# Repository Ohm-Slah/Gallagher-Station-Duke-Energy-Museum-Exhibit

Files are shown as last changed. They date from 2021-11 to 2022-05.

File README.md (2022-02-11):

# Gallagher-Station-Museum-Exhibit
 

A code repository for the Duke Energy funded exhibit at the Padgett Museum of the Gallagher Station, created by Purdue Polytechnic SoET students. This repository is only for the use of and contributed by these students. However, this information is for public viewing and usage. Any unwarranted pull-requests from unathorized individuals will be rejected, as this is to document the final product as-is. All code is under no licensure and is open for usage in the public domain. 

0607_ky_gallagher_station_plant

# What is this?
The Duke Energy Gallagher Station is located in New Albany, IN, and was a power generating facility that was of tremendous aid in powering Southern Indiana from 1958 until decommissioning in June of 2021. Duke Energy proposed the creation of an interactive museum exhibit representing the operation of a coal-fired power plant, with focus on the control system within the display. 

This project will be located at the Padgett Museum in New Albany, IN. The showcase will educate users on energy production control using older and current technologies and incorporating donated equipment from the Gallagher Station. The interactive exhibit will primarily be used by senior museum guests during normal operating hours of the Padgett Museum for an average of XX amount of time, and will not require training or previous knowledge of power systems to interact with it. This project must safely fit into the designated area of the museum without obstructing walking paths or needing to modify the surrounding environment. This project must be capable of being moved to a school and interacted with by a younger audience.

The code running on the Arduino Mega was written on a VSCode environment compiled and linked with the extension PlatformIO.

The code running on the ATTiny4313 controlling the 7-segment display is writen, compiled, and linked in the Arduino IDE.

# Folder Structure
The [src folder](https://github.com/Ohm-Slah/Gallagher-Station-Duke-Energy-Museum-Exhibit/tree/main/src) contains all cpp files to run on the Arduino Mega.

The [include folder](https://github.com/Ohm-Slah/Gallagher-Station-Duke-Energy-Museum-Exhibit/tree/main/include) contains all c header files used on Arduino Mega.

The [pi folder](https://github.com/Ohm-Slah/Gallagher-Station-Duke-Energy-Museum-Exhibit/tree/main/pi) contains the python code running on the raspberry pi.

The [pictures folder](https://github.com/Ohm-Slah/Gallagher-Station-Duke-Energy-Museum-Exhibit/tree/main/Pictures) contains pictures used in this repository.

The proc folder is no longer used, but is there for reference from another version of code on the Raspberry Pi.

# Proof of Concept Prototype
The proof of [concept prototype code](https://github.com/Ohm-Slah/Gallagher-Station-Duke-Energy-Museum-Exhibit/tree/Proof-of-Concept-Prototype) has been left as a seperate branch in Github, and you can view the project as how it was before any polish whatsoever. In the proof of concept for the method of playing videos at the request of a microcontroller, the program chosen initially was processing3 on Raspberry Pi. This was written in Java and worked well on a PC, however when running on a Raspberry Pi, the framerate dipped drastically. After a great deal of debugging and research, the final decision was to use OMXPlayer on Raspberry Pi programmed in Python. This switch to OMXPlayer was not realized until after the proof of concept prototype.
The proof of concept was also only programmed initially to showcase a rudimentary version of phases 0, 1, & 2, as well as the failure and completion routines. This code also showed the functionality of a stepper motor designed into a donated Gallagher Station gauge in place of a phase 3. There was no phase 4 written.

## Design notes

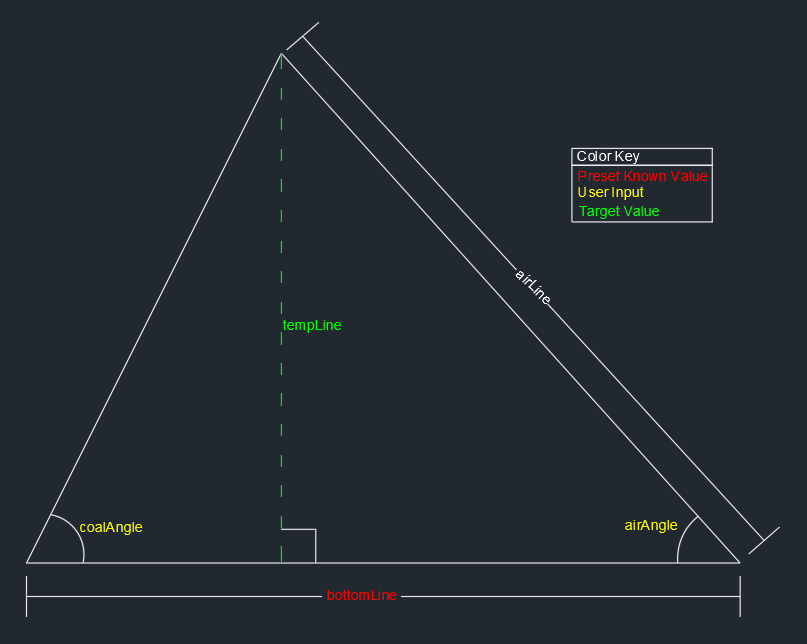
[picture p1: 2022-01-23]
Pictures/phase_one_conceptual.png

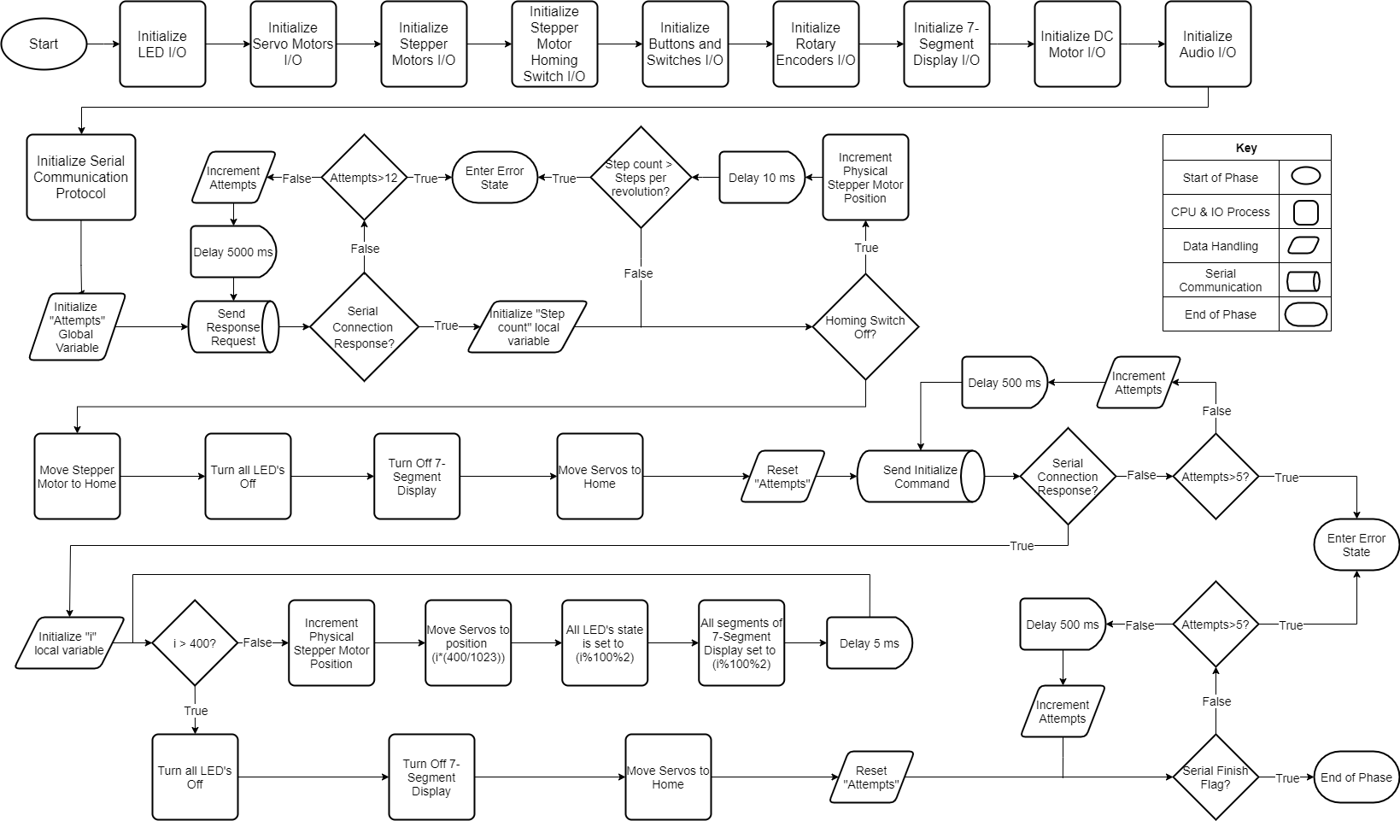
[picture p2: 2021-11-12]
Pictures/Gallagher_Code_Flow_Chart-Initialization.drawio.png

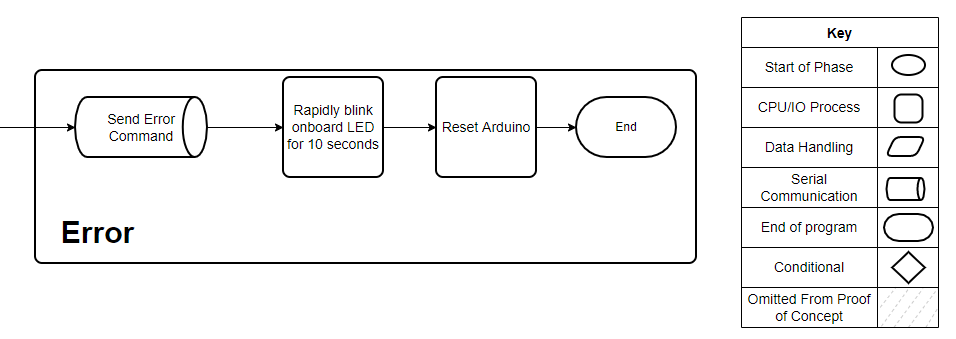
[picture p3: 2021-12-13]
Pictures/flowerror.PNG

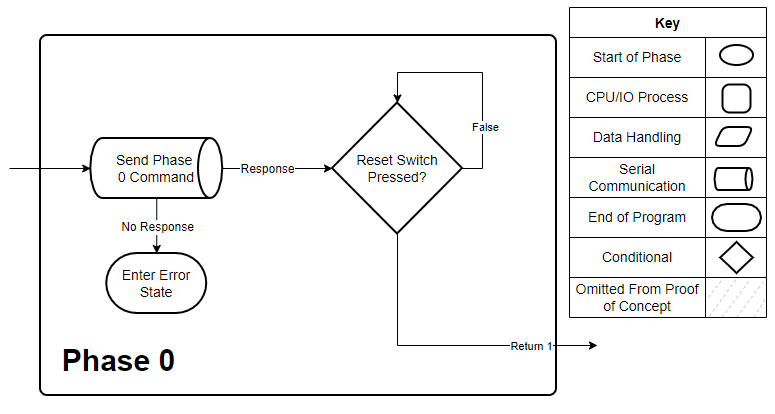
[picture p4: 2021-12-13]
Pictures/flowp0.PNG

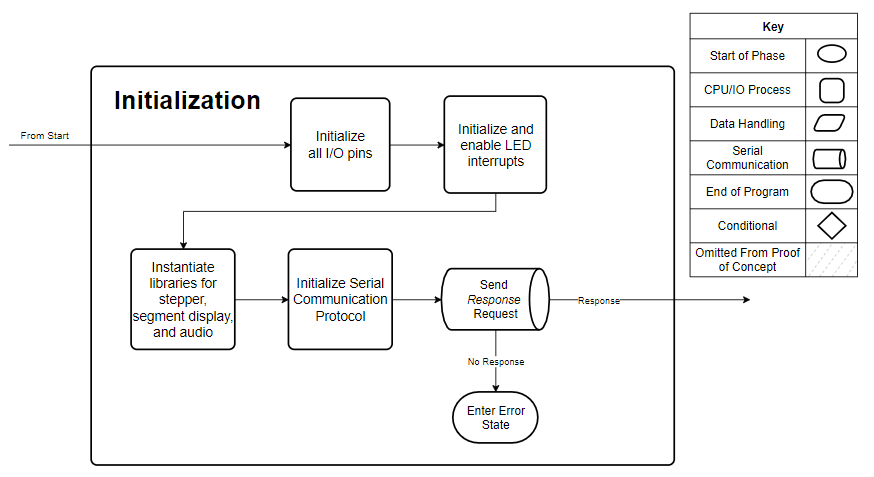
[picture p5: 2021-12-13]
Pictures/flowinit.PNG

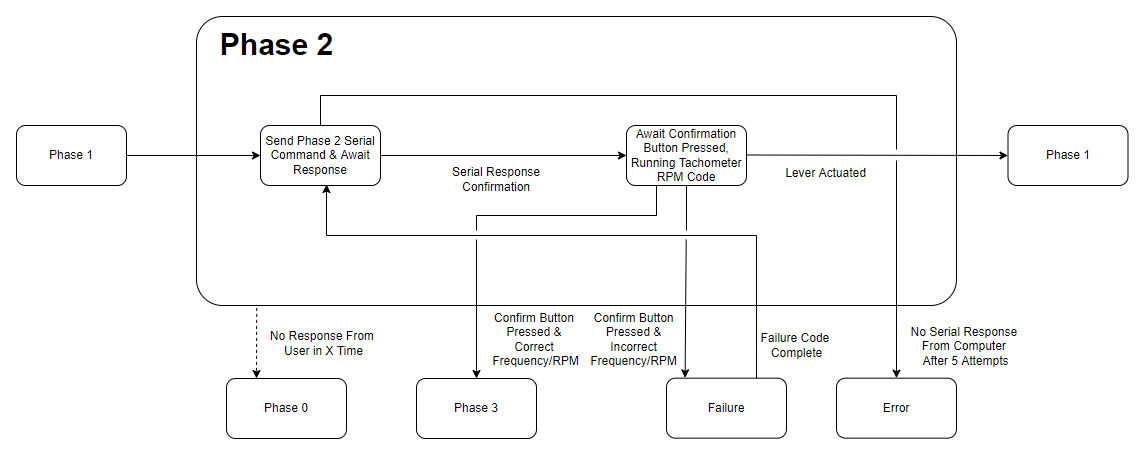
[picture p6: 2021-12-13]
Pictures/stphase2.PNG

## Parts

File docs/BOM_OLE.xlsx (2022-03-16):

 |  |  |  | DWG 1110 BILL OF MATERIALS (BOM)
DWG 1100 BILL OF MATERIALS (BOM) |  |  |  | IDENTIFIER | DESCRIPTION | PART #
IDENTIFIER | DESCRIPTION | PART # | LINK | M1 | SERVO MOTOR | SER-M-001
U1 | ARDUINO MEGA 2560 ATMEGA2560 | A000067 | https://www.digikey.com/en/products/detail/arduino/A000067/2639006 | M2 | SERVO MOTOR | SER-M-001
U2 | MICRO-SD CARD MODULE FOR ARDUINO | DFR0229 | https://www.digikey.com/en/products/detail/dfrobot/DFR0229/6588460 | U4 | ROTARY ENCODER | 288T232R161A1
J1 | CONN HEADER VERT 12POS 2.5MM | 533751210 | https://www.digikey.com/en/products/detail/molex/0533751210/3263206?s=N4IgTCBcDaIAwFYDMSDsCCMYNxAXQF8g | U5 | ROTARY ENCODER | 288T232R161A1
J23 | CONN HEADER VERT 11POS 2.5MM | 533751110 | https://www.digikey.com/en/products/detail/molex/0533751110/3263205?s=N4IgTCBcDaIAwFYDMSDsCCMW4gLoF8g | U6 | ROTARY ENCODER | 288T232R161A1
J6 | CONN HEADER VERT 7POS 2.5MM | 533750710 | https://www.digikey.com/en/products/detail/molex/0533750710/2421228?s=N4IgTCBcDaIAwFYDMSDsC6oIxxAXQF8g | U7 | ROTARY ENCODER | 288T232R161A1
J9 | CONN HEADER VERT 7POS 2.5MM | 533750710 | https://www.digikey.com/en/products/detail/molex/0533750710/2421228?s=N4IgTCBcDaIAwFYDMSDsC6oIxxAXQF8g | J2 | 3-PIN MALE MOLEX CONNECTOR | 3-M-MOLEX
J41 | CONN HEADER VERT 5POS 2.5MM | 533750510 | https://www.digikey.com/en/products/detail/molex/0533750510/2421211?s=N4IgTCBcDaIAwFYDMSDsDEEY4gLoF8g | J3 | 3-PIN MALE MOLEX CONNECTOR | 3-M-MOLEX
J15 | CONN HEADER VERT 2POS 2.5MM | 533750210 | https://www.digikey.com/en/products/detail/molex/0533750210/2405348?s=N4IgTCBcDaIAwFYDMSDsC5gIxxAXQF8g | J4 | 3-PIN MALE MOLEX CONNECTOR | 3-M-MOLEX
J47 | CONN HEADER VERT 2POS 2.5MM | 533750210 | https://www.digikey.com/en/products/detail/molex/0533750210/2405348?s=N4IgTCBcDaIAwFYDMSDsC5gIxxAXQF8g | J5 | 3-PIN MALE MOLEX CONNECTOR | 3-M-MOLEX
J27 | CONN HEADER VERT 2POS 2.5MM | 533750210 | https://www.digikey.com/en/products/detail/molex/0533750210/2405348?s=N4IgTCBcDaIAwFYDMSDsC5gIxxAXQF8g | J7 | 3-PIN MALE MOLEX CONNECTOR | 3-M-MOLEX
J29 | CONN HEADER VERT 2POS 2.5MM | 533750210 | https://www.digikey.com/en/products/detail/molex/0533750210/2405348?s=N4IgTCBcDaIAwFYDMSDsC5gIxxAXQF8g | J8 | 3-PIN MALE MOLEX CONNECTOR | 3-M-MOLEX
J31 | CONN HEADER VERT 2POS 2.5MM | 533750210 | https://www.digikey.com/en/products/detail/molex/0533750210/2405348?s=N4IgTCBcDaIAwFYDMSDsC5gIxxAXQF8g | CABLE_001 | REFFERENCE DRAWING 1120
J48 | CONN HEADER VERT 2POS 2.5MM | 533750210 | https://www.digikey.com/en/products/detail/molex/0533750210/2405348?s=N4IgTCBcDaIAwFYDMSDsC5gIxxAXQF8g | CABLE_003 | REFFERENCE DRAWING 1120
J33 | CONN HEADER VERT 2POS 2.5MM | 533750210 | https://www.digikey.com/en/products/detail/molex/0533750210/2405348?s=N4IgTCBcDaIAwFYDMSDsC5gIxxAXQF8g
H1 | HEX STANDOFF THREADED M2.5 | 971050154 | https://www.digikey.com/en/products/detail/würth-elektronik/971050154/9488600 | DWG 1111 BILL OF MATERIALS (BOM)
H2 | HEX STANDOFF THREADED M2.6 | 971050154 | https://www.digikey.com/en/products/detail/würth-elektronik/971050154/9488600 | IDENTIFIER | DESCRIPTION | PART #
H3 | HEX STANDOFF THREADED M2.7 | 971050154 | https://www.digikey.com/en/products/detail/würth-elektronik/971050154/9488600 | J28 | 2-PIN MALE MOLEX CONNECTOR | 2-M-MOLEX
H4 | HEX STANDOFF THREADED M2.8 | 971050154 | https://www.digikey.com/en/products/detail/würth-elektronik/971050154/9488600 | J30 | 2-PIN MALE MOLEX CONNECTOR | 2-M-MOLEX
U3 | CUSTOM JLC PCB | JLC01 | https://www.digikey.com/en/products/detail/molex/0533750210/2405348?s=N4IgTCBcDaIAwFYDMSDsC5gIxxAXQF8g | J32 | 2-PIN MALE MOLEX CONNECTOR | 2-M-MOLEX
CABLE_001 | REFFERENCE DRAWING 1120 |  |  | J49 | 2-PIN MALE MOLEX CONNECTOR | 2-M-MOLEX
CABLE_002 | REFFERENCE DRAWING 1120 |  |  | S1 | NO-PUSH BUTTON | PB-001
CABLE_003 | REFFERENCE DRAWING 1120 |  |  | S2 | NO-PUSH BUTTON | PB-002
CABLE_006 | REFFERENCE DRAWING 1121 |  |  | S3 | NO-PUSH BUTTON | PB-003
CABLE_010 | REFFERENCE DRAWING 1121 |  |  | S4 | NO-PUSH BUTTON | PB-004
CABLE_012 | REFFERENCE DRAWING 1121 |  |  | CABLE_012 | REFFERENCE DRAWING 1121
CABLE_013 | REFFERENCE DRAWING 1122 |  |  | CABLE_013 | REFFERENCE DRAWING 1122
CABLE_014 | REFFERENCE DRAWING 1122 |  |  | CABLE_014 | REFFERENCE DRAWING 1122
CABLE_015 | REFFERENCE DRAWING 1122 |  |  | CABLE_022 | REFFERENCE DRAWING 1123
CABLE_018 | REFFERENCE DRAWING 1122
CABLE_021 | REFFERENCE DRAWING 1123 |  |  | DWG 1610 BILL OF MATERIALS (BOM)
CABLE_022 | REFFERENCE DRAWING 1123 |  |  | IDENTIFIER | DESCRIPTION | PART #
 |  |  |  | J37 | 2-PIN MALE MOLEX CONNECTOR | 2-M-MOLEX
 | DWG 1120 BILL OF MATERIALS (BOM) |  |  | DS1 | 60W LED LIGHT-BULB | LED-60
IDENTIFIER | DESCRIPTION | PART # |  | CABLE_016 | REFFERENCE DRAWING 1620
J1 | 12-PIN ON-BOARD MALE CRIMP CONNECTOR | 51163-1200 |  | CABLE_017 | REFFERENCE DRAWING 1620
J2 | 3-PIN FEMALE MOLEX CONNECTOR | 3-F-MOLEX |  | DWG 1210 BILL OF MATERIALS (BOM)
J3 | 3-PIN FEMALE MOLEX CONNECTOR | 3-F-MOLEX |  | IDENTIFIER | DESCRIPTION | PART #
J4 | 3-PIN FEMALE MOLEX CONNECTOR | 3-F-MOLEX |  | U7 | HOMING SWITCH | Z6535-ND
J5 | 3-PIN FEMALE MOLEX CONNECTOR | 3-F-MOLEX |  | J14 | 4-PIN MALE MOLEX CONNECTOR | 4-M-MOLEX
J6 | 7-PIN ON-BOARD MALE CRIMP CONNECTOR | 53375-0710 |  | J12 | 7-PIN MALE MOLEX CONNECTOR | 7-M-MOLEX
J7 | 3-PIN FEMALE MOLEX CONNECTOR | 3-F-MOLEX |  | M3 | DC MOTOR | 2790-PC280LG-302-ND
J8 | 3-PIN FEMALE MOLEX CONNECTOR | 3-F-MOLEX |  | M4 | STEPPER MOTOR | 1568-1105-ND
J9 | 7-PIN ON-BOARD MALE CRIMP CONNECTOR | 53375-0710 |  | CABLE_004 | REFFERENCE DRAWING 1220
J10 | 7-PIN ON-BOARD FEMALE CRIMP CONNECTOR | 51163-0700 |  | CABLE_005 | REFFERENCE DRAWING 1220
 | DWG 1121 BILL OF MATERIALS (BOM) |  |  | DWG 1510 BILL OF MATERIALS (BOM)
IDENTIFIER | DESCRIPTION | PART # |  | IDENTIFIER | DESCRIPTION | PART #
J15 | 2-Pin MALE MOLEX MINI-LOCK CONNECTOR | 53375-0210 |  | J18 | 2-PIN MALE MOLEX CONNECTOR | 2-M-MOLEX
J16 | 2-PIN FEMALE MOLEX CONNECTOR | 2-F-MOLEX |  | J20 | 2-PIN MALE MOLEX CONNECTOR | 2-M-MOLEX
J23 | 11-PIN MALE MOLEX MINI-LOCK CONNECTOR | 53375-1210 |  | J22 | 2-PIN MALE MOLEX CONNECTOR | 2-M-MOLEX
J24 | 11-PIN FEMALE MOLEX CONNECTOR | 11-F-MOLEX |  | LS1 | VISATON 8-OHM SPEAKER | K 64 WP - 8 OHM
J27 | 2-PIN MALE MOLEX MINI-LOCK CONNECTOR | 53375-0210 |  | LS2 | VISATON 8-OHM SPEAKER | K 64 WP - 8 OHM
J28 | 2-PIN FEMALE MOLEX CONNECTOR | 2-F-MOLEX |  | LS3 | VISATON 8-OHM SPEAKER | K 64 WP - 8 OHM
 |  |  |  | CABLE_007 | REFFERENCE DRAWING 1520
 | DWG 1122 BILL OF MATERIALS (BOM) |  |  | CABLE_008 | REFFERENCE DRAWING 1520
IDENTIFIER | DESCRIPTION | PART # |  | CABLE_009 | REFFERENCE DRAWING 1520
J29 | 2-PIN ON-BOARD MALE CRIMP CONNECTOR | 53375-0210
J30 | 2-PIN FEMALE MOLEX CONNECTOR | 2-F-MOLEX |  | DWG 1210 BILL OF MATERIALS (BOM)
J31 | 2-PIN ON-BOARD MALE CRIMP CONNECTOR | 53375-0210 |  | IDENTIFIER | DESCRIPTION | PART #
J32 | 2-PIN FEMALE MOLEX CONNECTOR | 2-F-MOLEX |  | U7 | OMRON ELECTRONICS HOMING SWITCH | EE-SX4162-P1-Z
J33 | 2-PIN ON-BOARD MALE CRIMP CONNECTOR | 53375-0210 |  | J14 | 2-PIN FEMALE MOLEX CONNECTOR | 2-F-MOLEX
J34 | 2-PIN FEMALE MOLEX CONNECTOR | 2-F-MOLEX |  | J12 | 4-PIN FEMALE MOLEX CONNECTOR | 4-F-MOLEX
J41 | 5-PIN ON-BOARD MALE CRIMP CONNECTOR | 53375-0510 |  | J51 | 3-PIN FEMALE MOLEX CONNECTOR | 3-F-MOLEX
J42 | 5-PIN FEMALE MOLEX CONNECTOR | 5-F-MOLEX |  | M3 | JOHNSON MOTOR DC MOTOR | PC280LG-302
 |  |  |  | M4 | SPARKFUN STEPPER MOTOR | ROB-09238
 | DWG 1123 BILL OF MATERIALS (BOM) |  |  | CABLE_004 | REFFERENCE DRAWING 1220
IDENTIFIER | DESCRIPTION | PART # |  | CABLE_005 | REFFERENCE DRAWING 1220
J46 | 2-PIN MALE MOLEX MINI-LOCK CONNECTOR | 53375-0210
J47 | 2-PIN FEMALE MOLEX CONNECTOR | 2-F-MOLEX |  | DWG 1110 BILL OF MATERIALS (BOM)
J48 | 2-PIN MALE MOLEX MINI-LOCK CONNECTOR | 53375-0210 |  | IDENTIFIER | DESCRIPTION | PART #
J49 | 2-PIN FEMALE MOLEX CONNECTOR | 2-F-MOLEX |  | M1 | ADAFRUIT SERVO MOTOR | 154
 |  |  |  | M2 | ADAFRUIT SERVO MOTOR | 154
DWG 1200 BILL OF MATERIALS (BOM) |  |  |  | U4 | CTS ELECTRONICS ROTARY ENCODER | 288T232R161A1
IDENTIFIER | DESCRIPTION | PART # | LINK | U5 | CTS ELECTRONICS ROTARY ENCODER | 288T232R161A1
U4 | DRV8801 DC MOTOR DRIVER CARRIER | 2136 | https://www.digikey.com/en/products/detail/pololu-corporation/2136/10450430?s=N4IgTCBcDaICICUBqAOFAGAjCAugXyA | U6 | CTS ELECTRONICS ROTARY ENCODER | 288T232R161A1
U5 | A4988 STEPPER DRIVER | 1182 | https://www.digikey.com/en/products/detail/pololu-corporation/1182/10450403 | U7 | CTS ELECTRONICS ROTARY ENCODER | 288T232R161A1
U6 | CUSTOM JLC PCB | JLC02 |  | J2 | 3-PIN MALE MOLEX CONNECTOR | 3-M-MOLEX
J11 | CONN HEADER VERT 7POS 2.5MM | 533750710 | https://www.digikey.com/en/products/detail/molex/0533750710/2421228?s=N4IgTCBcDaIAwFYDMSDsC6oIxxAXQF8g | J3 | 3-PIN MALE MOLEX CONNECTOR | 3-M-MOLEX
J10 | CONN HEADER VERT 7POS 2.5MM | 533750710 | https://www.digikey.com/en/products/detail/molex/0533750710/2421228?s=N4IgTCBcDaIAwFYDMSDsC6oIxxAXQF8g | J4 | 3-PIN MALE MOLEX CONNECTOR | 3-M-MOLEX
J13 | CONN HEADER VERT 2POS 2.5MM | 533750210 | https://www.digikey.com/en/products/detail/molex/0533750210/2405348?s=N4IgTCBcDaIAwFYDMSDsC5gIxxAXQF8g | J5 | 3-PIN MALE MOLEX CONNECTOR | 3-M-MOLEX
J43 | CONN HEADER VERT 5POS 2.5MM | 533750510 | https://www.digikey.com/en/products/detail/molex/0533750510/2421211?s=N4IgTCBcDaIAwFYDMSDsDEEY4gLoF8g | J7 | 3-PIN MALE MOLEX CONNECTOR | 3-M-MOLEX
H1 | HEX STANDOFF THREADED M2.5 | 971050154 | https://www.digikey.com/en/products/detail/würth-elektronik/971050154/9488600 | J8 | 3-PIN MALE MOLEX CONNECTOR | 3-M-MOLEX
H2 | HEX STANDOFF THREADED M2.5 | 971050154 | https://www.digikey.com/en/products/detail/würth-elektronik/971050154/9488600 | CABLE_001 | REFFERENCE DRAWING 1120
H3 | HEX STANDOFF THREADED M2.5 | 971050154 | https://www.digikey.com/en/products/detail/würth-elektronik/971050154/9488600 | CABLE_003 | REFFERENCE DRAWING 1120
H4 | HEX STANDOFF THREADED M2.5 | 971050154 | https://www.digikey.com/en/products/detail/würth-elektronik/971050154/9488600
CABLE_002 | REFFERENCE DRAWING 1120
CABLE_004 | REFFERENCE DRAWING 1220
CABLE_005 | REFFERENCE DRAWING 1220
CABLE_019 | REFFERENCE DRAWING 1220
 | DWG 1220 BILL OF MATERIALS (BOM)
IDENTIFIER | DESCRIPTION | PART #
J11 | 7-PIN MALE MOLEX MINI-LOCK CONECTOR | 53375-0710
J12 | 4-PIN FEMALE MOLEX CONNECTOR | 4-F-MOLEX
J51 | 3-PIN FEMALE MOLEX CONNECTOR | 3-F-MOLEX
J13 | 2-PIN MALE MOLEX MINI-LOCK CONECTOR | 53375-0210
J14 | 4-PIN FEMALE MOLEX CONNECTOR | 4-F-MOLEX
J40 | 5-PIN MALE MOLEX MINI-LOCK CONECTOR | 53375-0510
J43 | 5-PIN FEMALE MOLEX CONNECTOR | 5-F-MOLEX
DWG 1300 BILL OF MATERIALS (BOM)
IDENTIFIER | DESCRIPTION | PART # | LINK
U7 | AVR SERIES MICROCONTROLLER IC 8-BIT | ATTINY4313-PU | https://www.digikey.com/en/products/detail/microchip-technology/ATTINY4313-PU/2271083
U8 | UNIQUE GALLAGHER STATION 7-SEGMENT PASSIVE DISPLAY BOARD | GS-7-SEG
U9 | CUSTOM PROTO BOARD LAYOUT | 2670 | https://www.digikey.com/en/products/detail/adafruit-industries-llc/2670/7244957
J42 | CONNECTOR HEADER THROUGH HOLE 5 POSITION | 533750510 | https://www.digikey.com/en/products/detail/molex/0533750510/2421211?s=N4IgTCBcDaIAwFYDMSDsDEEY4gLoF8g
R1 -> R15 | 150 OHMS ±1% 0.6W THROUGH HOLE RESISTOR | LR1F150R | https://www.digikey.com/en/products/detail/te-connectivity-passive-product/LR1F150R/3477523
Q1 -> Q7 | BIPOLAR (BJT) TRANSISTOR NPN 40 V 600 mA | 2N2222A | https://www.digikey.com/en/products/detail/diotec-semiconductor/2N2222A/13575189
CABLE_018 | REFFERENCE DRAWING 1122
DWG 1400 BILL OF MATERIALS (BOM)
IDENTIFIER | DESCRIPTION | PART # | LINK
U10 | CUSTOM JLC PCB | JLC03
J26 | CONN HEADER VERT 2POS 2.5MM | 533750210 | https://www.digikey.com/en/products/detail/molex/0533750210/2405348?s=N4IgTCBcDaIAwFYDMSDsC5gIxxAXQF8g
J24 | CONN HEADER VERT 11POS 2.5MM | 533751110 | https://www.digikey.com/en/products/detail/molex/0533751110/3263205?s=N4IgTCBcDaIAwFYDMSDsCCMW4gLoF8g
J50 -> J60 | CONN HEADER VERT 2POS 2.5MM | 533750210 | https://www.digikey.com/en/products/detail/molex/0533750210/2405348?s=N4IgTCBcDaIAwFYDMSDsC5gIxxAXQF8g
H1 -> H4 | HEX STANDOFF THREADED M2.5 | 971050154 | https://www.digikey.com/en/products/detail/würth-elektronik/971050154/9488600
Q8 -> Q18 | TRANS PNP 40V 0.2A TO-92 | 2N3906 | https://www.digikey.com/en/products/detail/stmicroelectronics/2N3906/603429
R16 -> R26 | RES 1 KOHMS 1/2W AXIAL | 273-1.0K-RC | https://www.digikey.com/en/products/detail/xicon/273-1-0K-RC/10485991
R27 -> R37 | RES 220 OHMS 1/2W AXIAL | HWCC122 | https://www.digikey.com/en/products/detail/nte-electronics-inc/HWCC122/11654401
CABLE_010 | REFFERENCE DRAWING 1121
CABLE_011 | REFFERENCE DRAWING 1420
 | DWG 1420 BILL OF MATERIALS (BOM)
IDENTIFIER | DESCRIPTION | PART #
J25 | 2-PIN ON-BOARD MALE CRIMP CONNECTOR | 53375-0210
J26 | 2-PIN FEMALE MOLEX CONNECTOR | 2-F-MOLEX
DWG 1500 BILL OF MATERIALS (BOM)
IDENTIFIER | DESCRIPTION | PART # | LINK
U11 | AMP AUDIO 3.7W CLASS D | 987 | https://www.digikey.com/en/products/detail/adafruit-industries-llc/987/5629428
U12 | IC OPAMP GP 2 CIRCUIT 8DIP | LM358AN/NOPB | https://www.digikey.com/en/products/detail/texas-instruments/LM358AN-NOPB/54928
U13 | AUX CABLE TO BARE COPPER WIRES | AUX-01
U14 | CUSTOM JLC PCB | JLC04
C1 & C2 | CAP ALUM 100UF 20% 16V RADIAL | UPJ1C101MED1TD | https://www.digikey.com/en/products/detail/nichicon/UPJ1C101MED1TD/3129347
J16 | CONNECTOR HEADER THROUGH HOLE 2 POSITION | 533750210 | https://www.digikey.com/en/products/detail/molex/0533750210/2405348
J17 | CONNECTOR HEADER THROUGH HOLE 2 POSITION | 533750210 | https://www.digikey.com/en/products/detail/molex/0533750210/2405348
J19 | CONNECTOR HEADER THROUGH HOLE 2 POSITION | 533750210 | https://www.digikey.com/en/products/detail/molex/0533750210/2405348
J21 | CONNECTOR HEADER THROUGH HOLE 2 POSITION | 533750210 | https://www.digikey.com/en/products/detail/molex/0533750210/2405348
J45 | CONNECTOR HEADER THROUGH HOLE 5 POSITION | 533750510 | https://www.digikey.com/en/products/detail/molex/0533750510/2421211?s=N4IgTCBcDaIAwFYDMSDsDEEY4gLoF8g
H1 -> H4 | HEX STANDOFF THREADED M2.5 | 971050154 | https://www.digikey.com/en/products/detail/würth-elektronik/971050154/9488600
CABLE_006 | REFFERENCE DRAWING 1121
CABLE_007 | REFFERENCE DRAWING 1520
CABLE_008 | REFFERENCE DRAWING 1520
CABLE_009 | REFFERENCE DRAWING 1520
CABLE_020 | REFFERENCE DRAWING 1520
 | DWG 1520 BILL OF MATERIALS (BOM)
IDENTIFIER | DESCRIPTION | PART #
J17 | 2-PIN ON-BOARD MALE CRIMP CONNECTOR | 53375-0210
J18 | 2-PIN FEMALE MOLEX CONNECTOR | 2-F-MOLEX
J19 | 2-PIN ON-BOARD MALE CRIMP CONNECTOR | 53375-0210
J20 | 2-PIN FEMALE MOLEX CONNECTOR | 2-F-MOLEX
J21 | 2-PIN ON-BOARD MALE CRIMP CONNECTOR | 53375-0210
J22 | 2-PIN FEMALE MOLEX CONNECTOR | 2-F-MOLEX
J44 | 5-PIN ON-BOARD MALE CRIMP CONNECTOR | 53375-0510
J45 | 5-PIN FEMALE MOLEX CONNECTOR | 5-F-MOLEX
DWG 1600 BILL OF MATERIALS (BOM)
IDENTIFIER | DESCRIPTION | PART # | LINK
U15 | SOLID STATE RELAY | AQH3213
U16 | CUSTOM JLC PCB | JLC04
R38 | RES 120 OHM 1% 0.6W AXIAL | LR1F120R | https://www.digikey.com/en/products/detail/te-connectivity-passive-product/LR1F120R/3477521
J34 | CONNECTOR HEADER THROUGH HOLE 2 POSITION | 533750210 | https://www.digikey.com/en/products/detail/molex/0533750210/2405348
J36 | CONNECTOR HEADER THROUGH HOLE 2 POSITION | 533750210 | https://www.digikey.com/en/products/detail/molex/0533750210/2405348
J38 | CONNECTOR HEADER THROUGH HOLE 2 POSITION | 533750210 | https://www.digikey.com/en/products/detail/molex/0533750210/2405348
H1 -> H4 | HEX STANDOFF THREADED M2.5 | 971050154 | https://www.digikey.com/en/products/detail/würth-elektronik/971050154/9488600
CABLE_015 | REFFERENCE DRAWING 1122
CABLE_016 | REFFERENCE DRAWING 1620
CABLE_017 | REFFERENCE DRAWING 1620
 | DWG 1620 BILL OF MATERIALS (BOM)
IDENTIFIER | DESCRIPTION | PART #
J36 | 2-PIN ON-BOARD MALE CRIMP CONNECTOR | 53375-0210
J37 | 2-PIN FEMALE MOLEX CONNECTOR | 2-F-MOLEX
J38 | 2-PIN ON-BOARD MALE CRIMP CONNECTOR | 53375-0210
J39 | 2-PIN FEMALE MOLEX CONNECTOR | 2-F-MOLEX
 | DWG 1800 BILL OF MATERIALS (BOM)
IDENTIFIER | DESCRIPTION | PART #
CABLE_017 | REFFERENCE DRAWING 1620
Monitor | HP DESKTOP MONITOR | L1702
PS1 | XP POWER +5V POWER SUPPLY | LCW35US05
PS2 | XP POWER +12V POWER SUPPLY | LCW35US12
PS3 | +5 RASPBERRY PI POWER SUPPLY | KSA-15E-051300HU
F1 | BEL FUSE 4A FUSE RATED | 5TT 4-R
F2 | LITTLEFUSE 1A FUSE RATED | 0232001.MX125P
F3 | LITTLEFUSE 1A FUSE RATED | 0232001.MX125P
F4 | LITTLEFUSE 0.15A FUSE RATED | 0239.150MXP
BUS_001 | PHOENIX CONTACT TERMINAL BLOCK | UT 2,5-QUATTRO
BUS_002 | PHOENIX CONTACT TERMINAL BLOCK | UT 2,5-QUATTRO
CABLE_011 | REFFERENCE DRAWING 1420
CABLE_019 | REFFERENCE DRAWING 1220
CABLE_020 | REFFERENCE DRAWING 1520
CABLE_021 | REFFERENCE DRAWING 1123

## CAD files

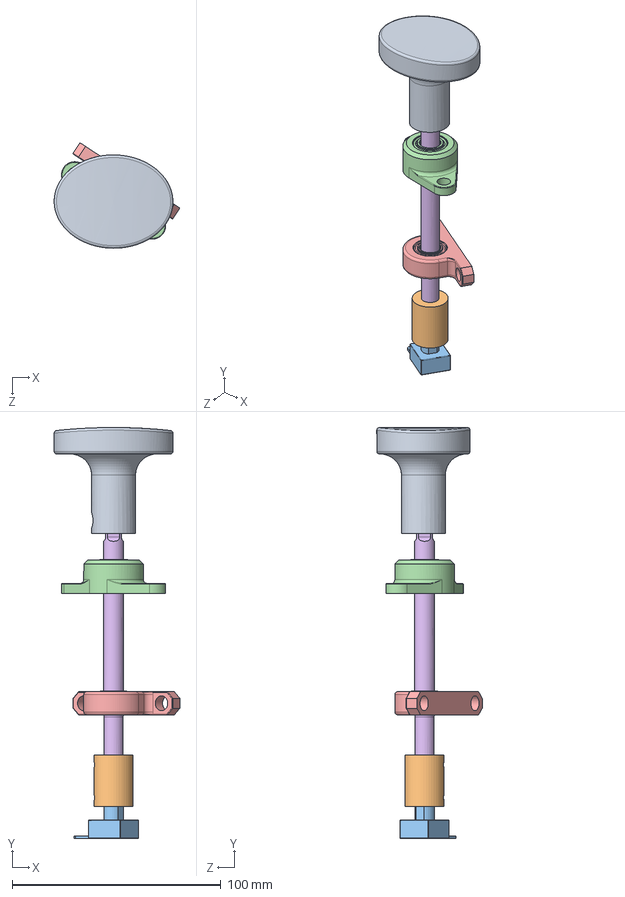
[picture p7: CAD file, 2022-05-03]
docs/mechanical/Group3_2022_GallagherStationExhibitRedDialAssembly.SLDASM
60.2 x 196.8 x 50.5 mm
GallagherRedDial
EncoderAttachmentPeice
RotaryEncoder
2820T35_Dry-Running Mounted Sleeve Bearing
4393N14_Dry-Running Mounted Sleeve Bearing
RedDialPole

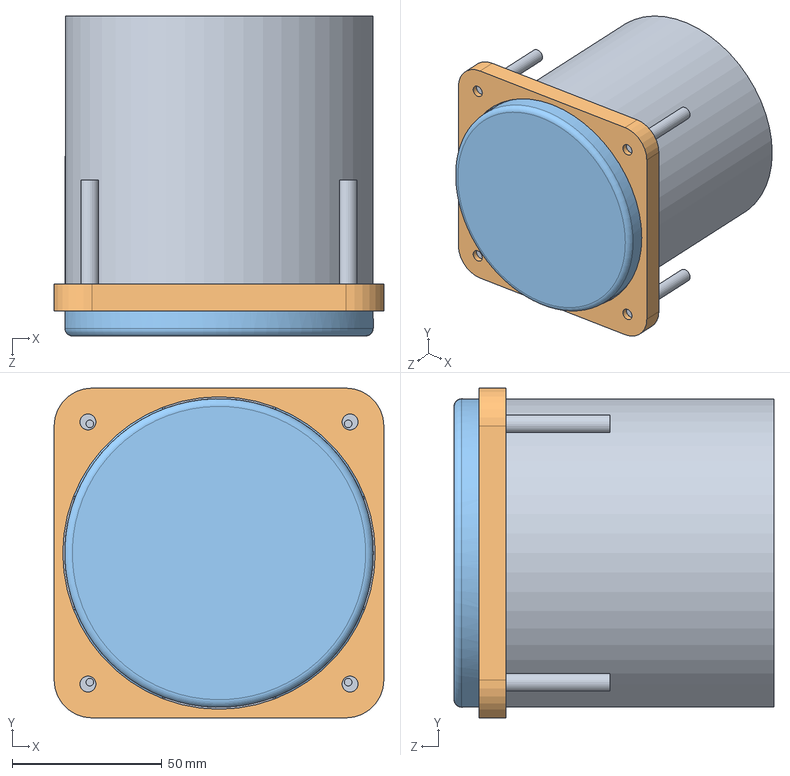
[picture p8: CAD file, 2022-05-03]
docs/mechanical/Group3_2022_GallagherStationExhibitGaugeAssembly.SLDASM
110.0 x 110.0 x 106.7 mm
GaugeOuterCase
GaugeFacePlate
GaugeGlass

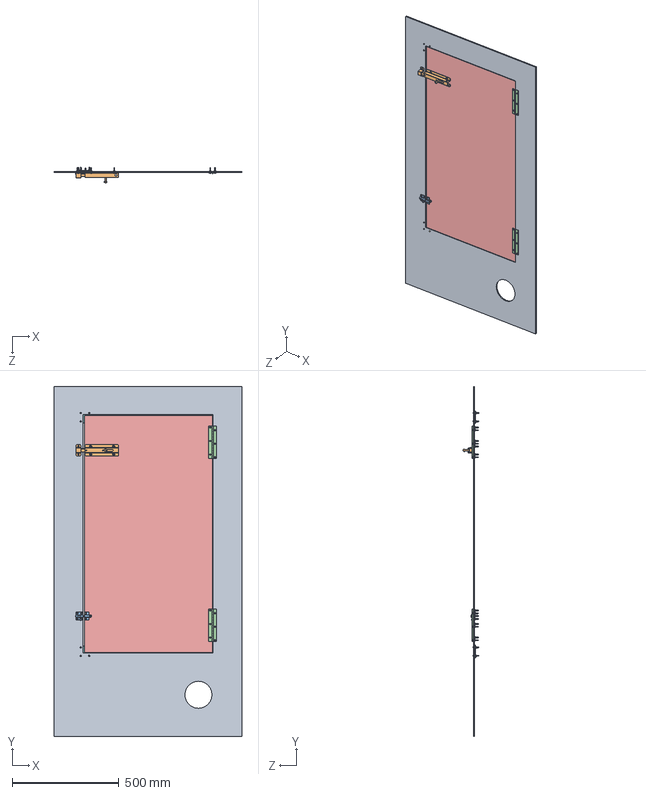
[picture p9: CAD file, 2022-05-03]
docs/mechanical/Group3_2022_GallagherStationExhibitDoorAssembly.SLDASM
879.7 x 1641.5 x 73.0 mm
back panal
1244A3_Padlockable Slide-Bolt Latch
1544N36_Self-Aligning Slide-Bolt Latch
1586A34_Surface-Mount Hinge with Holes x 2
door
90480A007_Low-Strength Steel Hex Nut x 31
91735A154_316 Stainless Steel Pan Head Phillips Screw x 31
Door Backstops x 2

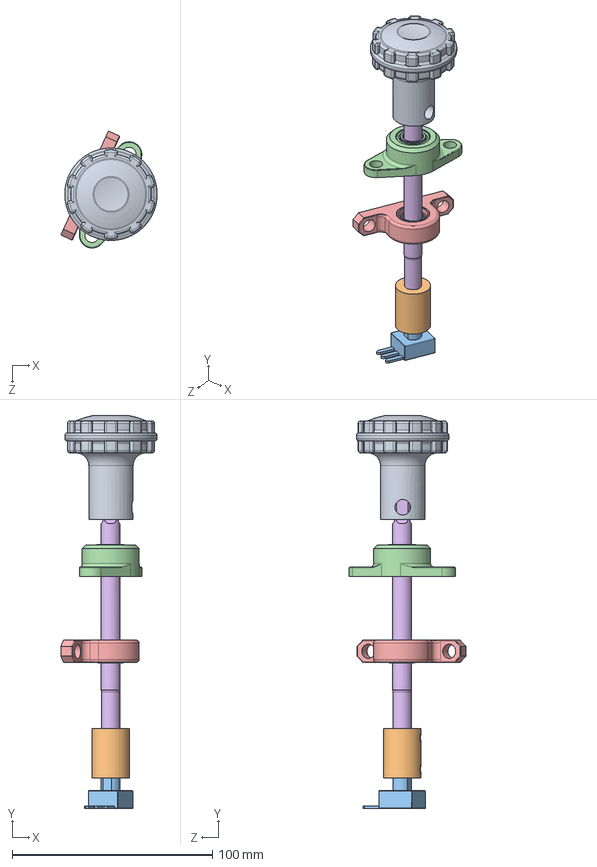
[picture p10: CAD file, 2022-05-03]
docs/mechanical/Group3_2022_GallagherStationExhibitBlackDialAssembly.SLDASM
48.2 x 196.4 x 58.5 mm
black knob (1)
EncoderAttachmentPeice
RotaryEncoder
2820T35_Dry-Running Mounted Sleeve Bearing
4393N14_Dry-Running Mounted Sleeve Bearing
RedDialPole

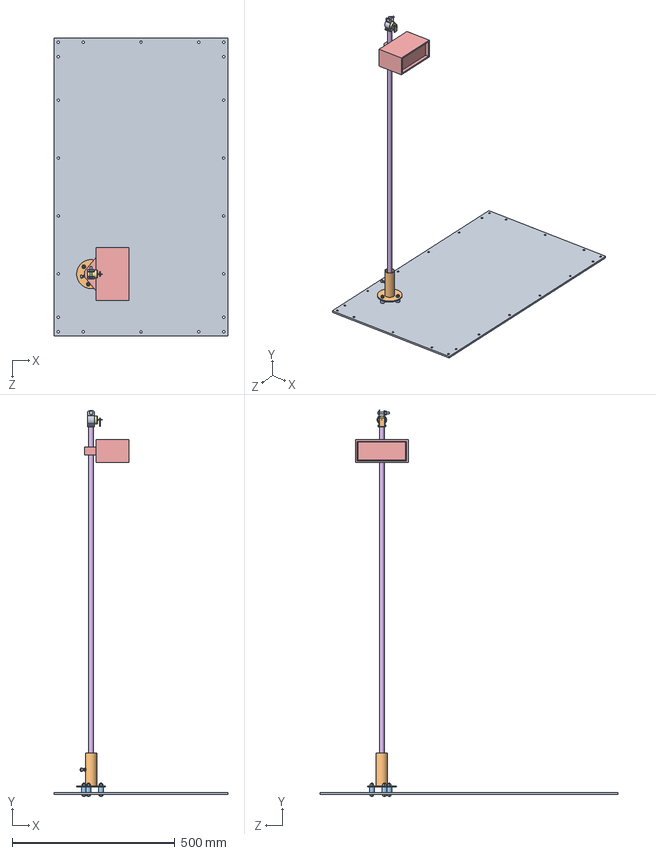
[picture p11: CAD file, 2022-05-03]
docs/mechanical/Group3_2022_GallagherStationExhibitBottomTachometerAssembly.SLDASM
533.4 x 1184.3 x 914.4 mm
bottom
2534T82_Clamp-on Framing Fitting
9213K57_Vibration-Damping Sandwich Mount with Stud x 3
95462A029_Medium-Strength Steel Hex Nut x 6
Tachometer
Tachpole
tachmotor
92949A832_18-8 Stainless Steel Button Head Hex Drive Screw
3006T52_Threaded-Rod-Mount Clamping Hanger
offsetweight

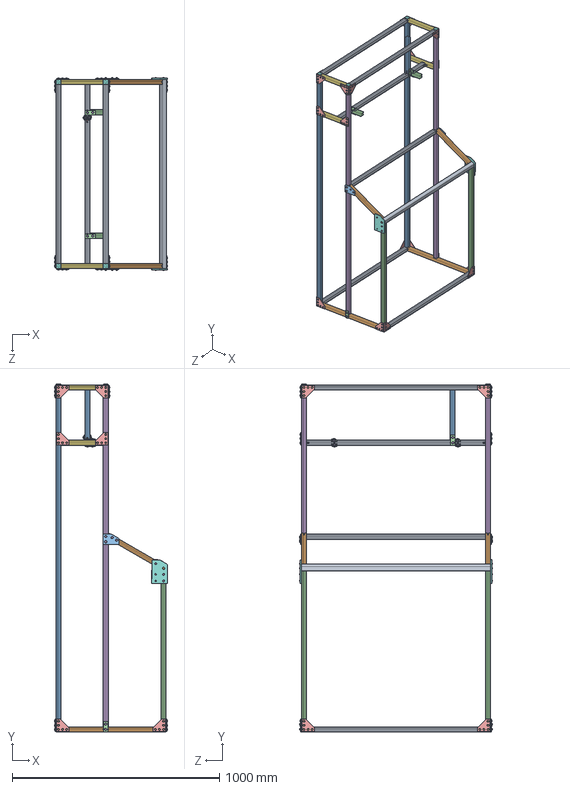
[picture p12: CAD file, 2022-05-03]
docs/mechanical/Group3_2022_GallagherStationExhibitFrame Assembly.SLDASM
547.2 x 1679.6 x 932.2 mm
34in Beam x 6
18.985in Beam x 2
65.96in Beam x 2
30.604in Beam x 2
47065T267_T-Slotted Framing x 20
64.98in Beam x 2
8in Beam x 4
30 Degree Angle Bracket x 2
60 degree cosmetic peice
12in Beam x 2
47065T329_T-Slotted Framing x 2
47065T255_T-Slotted Framing x 8
5537T315_T-Slotted Framing x 9
47065T139_T-Slotted Framing x 30
91770A253_Extra-Wide Truss Head Phillips Screws x 2
3136N252_T-Slotted Framing x 4
5537T651_T-Slotted Framing x 100
91306A757_Button Head Hex Drive Screws x 100
10in Beam
2.75in Beam x 2

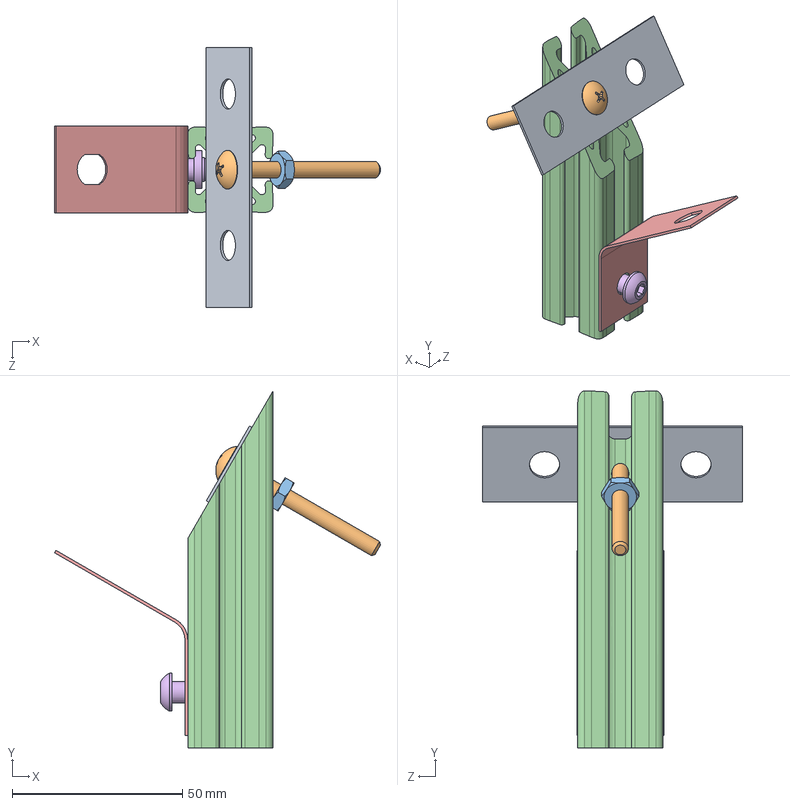
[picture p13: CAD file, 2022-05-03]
docs/mechanical/Group3_2022_GallagherStationExhibitRotary Encoder Support.SLDASM
95.7 x 104.8 x 76.2 mm
DialSupportPlate
91770A253_Extra-Wide Truss Head Phillips Screws
90480A011_Low-Strength Steel Hex Nut
Front Dial Support Beam
Rotary Encoder Angle Plate
47065T139_T-Slotted Framing

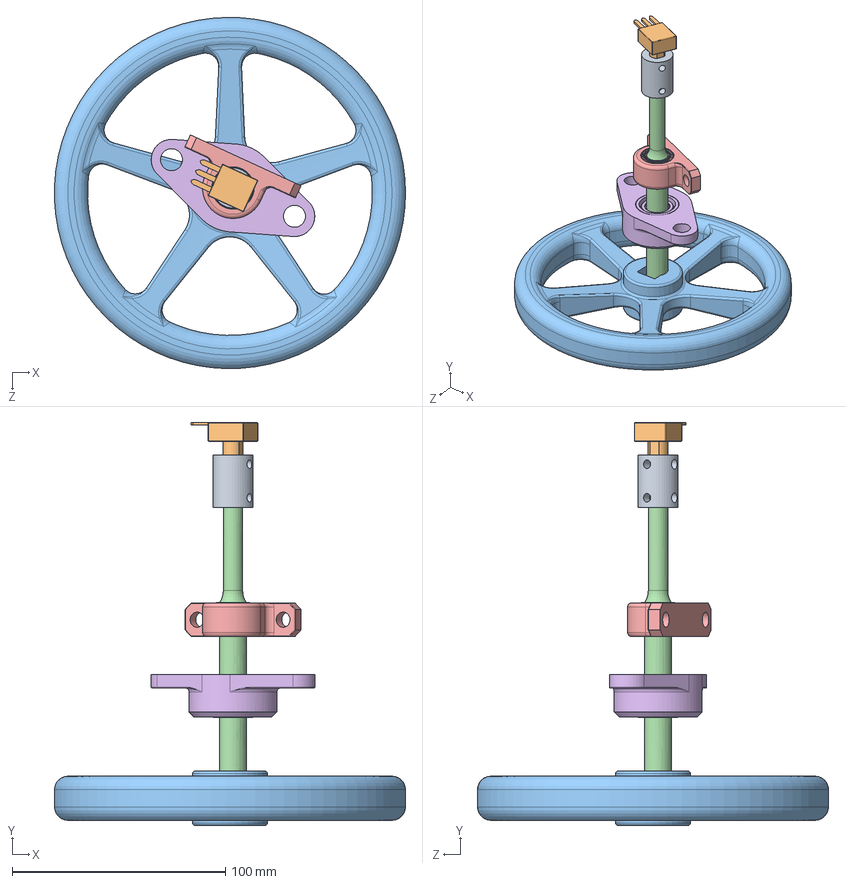
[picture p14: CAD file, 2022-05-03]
docs/mechanical/Group3_2022_GallagherStationExhibitHandWheelAssembly.SLDASM
164.7 x 189.1 x 164.7 mm
EncoderAttachmentPeice
RotaryEncoder
wheel2 (1)
wheelpole
4393N15_Dry-Running Mounted Sleeve Bearing
2820T36_Dry-Running Mounted Sleeve Bearing

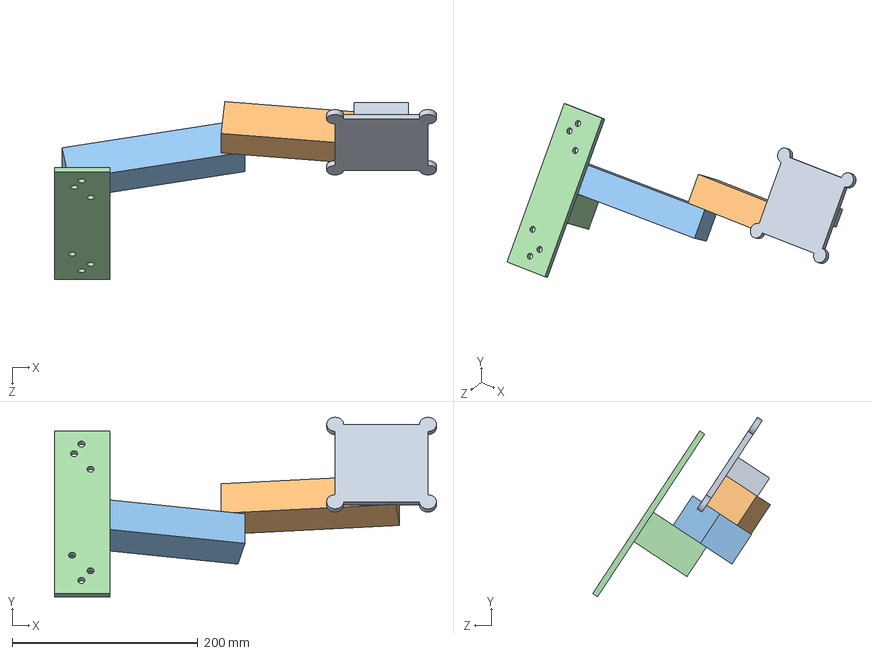
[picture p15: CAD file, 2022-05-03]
docs/mechanical/Group3_2022_GallagherStationExhibitMonitorMountAssembly.SLDASM
411.9 x 193.7 x 191.7 mm
Part14^MonitorMountAssembly
Part15^MonitorMountAssembly
Part16^MonitorMountAssembly
Part17^MonitorMountAssembly

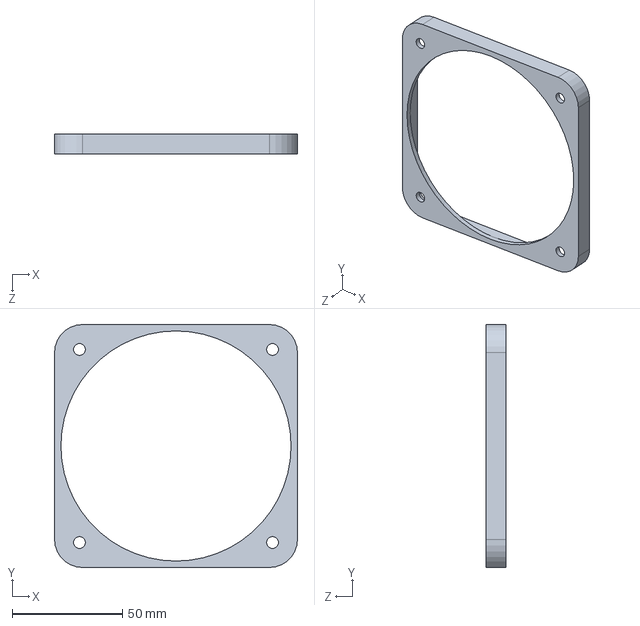
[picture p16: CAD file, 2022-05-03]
docs/mechanical/Group3_2022_GallagherStationExhibitGaugeFacePlate.SLDPRT
110.0 x 110.0 x 9.03 mm

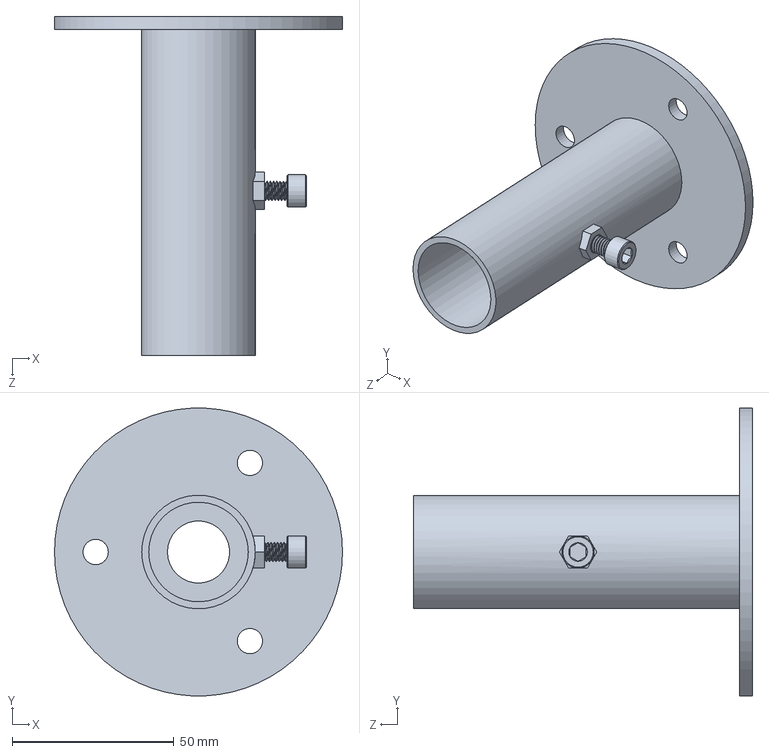
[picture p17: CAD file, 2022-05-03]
docs/mechanical/Group3_2022_GallagherStationExhibit2534T82_Clamp-on Framing Fitting.SLDPRT
88.9 x 88.8 x 104.6 mm

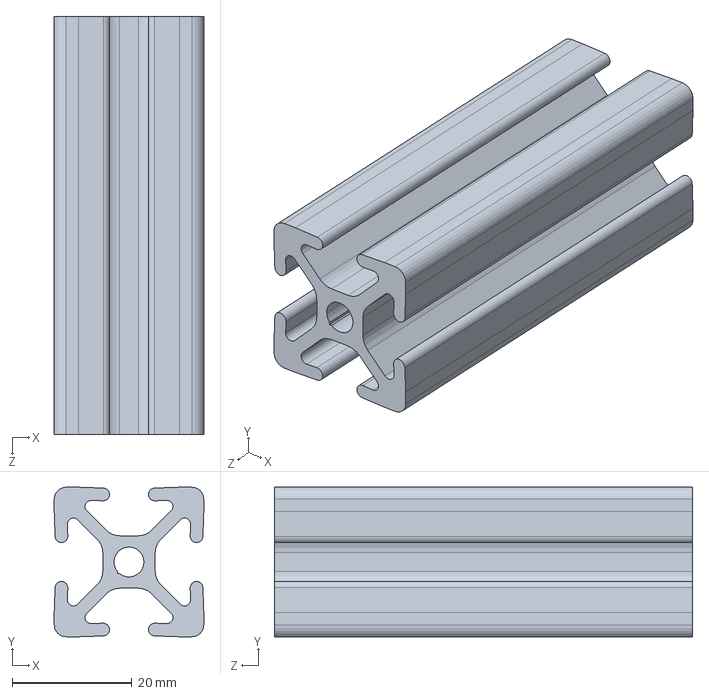
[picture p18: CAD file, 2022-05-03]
docs/mechanical/Group3_2022_GallagherStationExhibit2.75in Beam.SLDPRT
25.0 x 25.0 x 69.8 mm

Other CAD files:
docs/dwg/CABLES AND WIRE HARNESS CONNECTORS/1200_DWG.dwg
docs/electrical/dwg/1500.dwg
docs/dwg/CABLES AND WIRE HARNESS CONNECTORS/1160_DWG.dwg
docs/electrical/dwg/1210.dwg
docs/dwg/CABLES AND WIRE HARNESS CONNECTORS/1130_DWG.dwg
docs/electrical/dwg/1123.dwg
docs/dwg/CABLES AND WIRE HARNESS CONNECTORS/1190_DWG.dwg
docs/electrical/dwg/(old)CABLES AND WIRE HARNESS CONNECTORS/1120_DWG.dwg
docs/electrical/dwg/(old)CABLES AND WIRE HARNESS CONNECTORS/1130_DWG.dwg
docs/electrical/dwg/(old)CABLES AND WIRE HARNESS CONNECTORS/1140_DWG.dwg
docs/electrical/dwg/(old)CABLES AND WIRE HARNESS CONNECTORS/1150_DWG.dwg
docs/electrical/dwg/(old)CABLES AND WIRE HARNESS CONNECTORS/1150_DWG_recover.dwg
docs/electrical/dwg/(old)CABLES AND WIRE HARNESS CONNECTORS/1160_DWG.dwg
docs/electrical/dwg/(old)CABLES AND WIRE HARNESS CONNECTORS/1170_DWG.dwg
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

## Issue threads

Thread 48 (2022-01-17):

Rewrite rotary encoder code

Ohm-Slah, 2022-01-17:

Ohm-Slah, 2022-01-21:
Fixed in #53

Closed 2022-01-21.

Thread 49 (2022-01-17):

Rewrite 7-seg code

Ohm-Slah, 2022-01-17:

Ohm-Slah, 2022-01-21:
This would now include reverse engineering old 7-seg driver boards along with the hardware design to drive 'em.

Closed 2022-02-05.

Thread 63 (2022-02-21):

Review and revise wire harness drawings

FlyingBowser, 2022-02-21:
All wire harness drawings are in the docs -> dwg -> CABLE AND WIRE HARNESS CONNECTORS. These files need to be revised and updated

Ohm-Slah, 2022-03-01:
@Jack12COuch8 What is your progress on this?

FlyingBowser, 2022-03-07:
Connectors have been revised and edited for current PCB schematics. Closed Issue

Closed 2022-03-07.

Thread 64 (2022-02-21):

Add LED connectors endpoints (J50-J60)

FlyingBowser, 2022-02-21:
J50 to J60 are the connectors on the LED board, LEDs themselves have screw terminal endpoints and need schematic drawings to illustrate that

Closed 2022-02-28.

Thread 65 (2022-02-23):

Update Numbering scheme

FlyingBowser, 2022-02-23:
This was the heirarchy proposed in class: Just wanted to post it here for refference as something we need to do

DRAWING HEIRARCHY (NEW PROPOSED)
1x00-1x09: PCB AND ON-BOARD COMPONENTS
	-PCB layout, on-board components, BOM for components shown on sheet
1x10-1x19: OFF-BOARD COMPONENTS
	-motors, connectors, switches, encoders, etc.
1x20-1x29: CONNECTORS AND CABLES
	-cable details, connectors.

Heirarchy:
1100 - Arduino Board
1200 - Motor Board
1300 - 7-segment LED
1400 - System LEDs
1500 - Audio Amp
1600 - SSR
1700 - Raspberry Pi
1800 - Main power

FlyingBowser, 2022-03-05:
updated old schematic drawings to new numbers. new drawings will reflect new system

connectors are next to be changed

Closed 2022-03-07.

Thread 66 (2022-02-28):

Add endpoints for all drawings

FlyingBowser, 2022-02-28:
add endpoints for all board going to an external connector (motors or 7segment LED for example)

Ohm-Slah, 2022-03-10:
@FlyingBowser Where are you at with this?

FlyingBowser, 2022-03-10:
I am going to do 1100 endpoints today then do one or two sets per day to commit more time to details on different sets

Ohm-Slah, 2022-03-10:
Sounds good. Fyi, I have moved all BOM material to a centralized file to help with simplicity. The commit can be found here: [456dcd23a9117a93bf4793d457157b3c41bb55c1](https://github.com/Ohm-Slah/Gallagher-Station-Duke-Energy-Museum-Exhibit/commit/456dcd23a9117a93bf4793d457157b3c41bb55c1)
Thanks

FlyingBowser, 2022-03-13:
1100 and 1200 done, need reviewed

FlyingBowser, 2022-03-14:
All current drawings reviewed, currently working on 1310 and 1410

FlyingBowser, 2022-03-14:
Update: 1310 not needed

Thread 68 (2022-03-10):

Add 1320 DWG

Ohm-Slah, 2022-03-10:
Cable diagram for the 1300 dwg's are missing.
@Jack12COuch8 @FlyingBowser
Is this file not necessary? I'm pretty sure there's a cable going from Arduino board to 7-segment board, 4-wires on 5-pin connectors.

FlyingBowser, 2022-03-10:
That is correct there is a single cable, but it is a board- board cable and is referenced on drawing 112x. BOM on 1300 references correct drawing. 1320 is not necessary

Closed 2022-03-10.

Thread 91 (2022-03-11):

Flip wooden board

Ohm-Slah, 2022-03-11:

Closed 2022-03-15.

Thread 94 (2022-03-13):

Add 1700 (Raspberry Pi diagram) and 1800 (source power) to drawings

FlyingBowser, 2022-03-13:
1800 we technically already have through Jackson's fuse diagram. Needs to be refined for additional components.
1700 needs to be created in general

Closed 2022-03-24.

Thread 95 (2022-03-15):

Concatenate all BOM's

Ohm-Slah, 2022-03-15:
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
@Jack12COuch8 @FlyingBowser
Let's not do this please. Keep it all in the same file if you can.

FlyingBowser, 2022-03-15:
I merged the BOM into one file last night

Ohm-Slah, 2022-03-15:
Thank you

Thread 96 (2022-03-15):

Rename DWG 1110, 1111,  and 1610

Ohm-Slah, 2022-03-15:
Match naming scheme please. Go through them and change the file name listed in the readme as well.
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

Also, there are two existing 1800 drawings. Please delete one.

Closed 2022-03-16.

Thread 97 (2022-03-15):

Find non-Digikey Part Numbers

Ohm-Slah, 2022-03-15:
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
The image above shows one of your BOM's @FlyingBowser. The part # must be the manufacturing part #, and the 'ND' at the end tells me you are using Digikey part numbers. We got directly called out on this on the Gate 4 CDR, please fix this.

Closed 2022-03-16.

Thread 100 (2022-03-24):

Fix LED's that are not blinking

Ohm-Slah, 2022-03-24:

Closed 2022-04-21.

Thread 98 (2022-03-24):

Debug and fix stepper motor

Ohm-Slah, 2022-03-24:

Closed 2022-03-31.

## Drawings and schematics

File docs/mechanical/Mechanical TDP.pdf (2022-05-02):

8 | 7 | 6 | 5 | 4 | 3 | 1

D

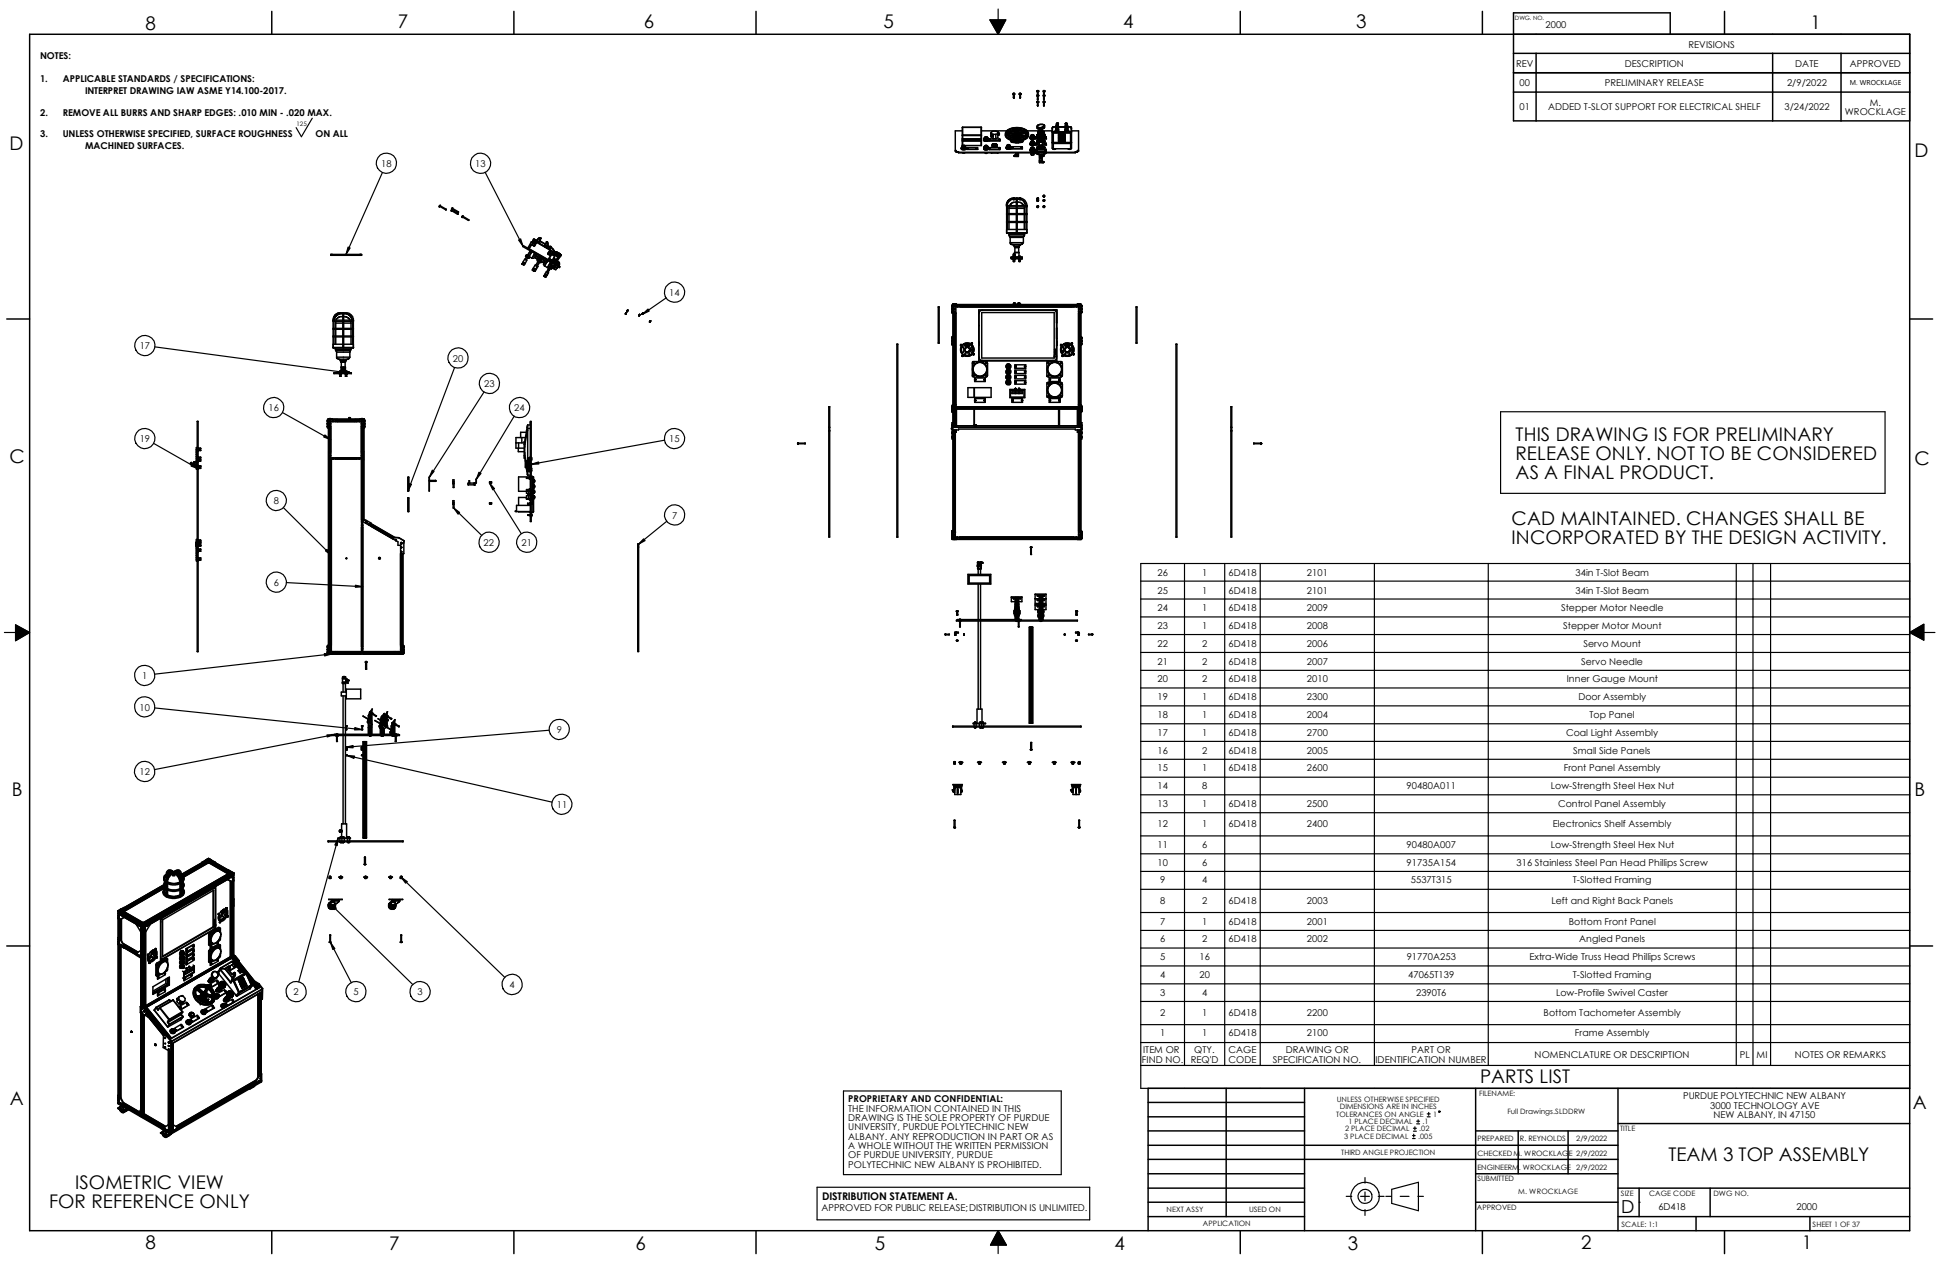
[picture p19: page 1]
ISOMETRIC VIEW; FOR REFERENCE ONLY; APPROVED FOR PUBLIC RELEASE;DISTRIBUTION IS UNLIMITED.; DISTRIBUTION STATEMENT A.; M. WROCKLAGE; DWG. NO.; NEXT ASSY; USED ON; APPROVED; SUBMITTED; REVISIONS; REV; DESCRIPTION; DATE; PRELIMINARY RELEASE; ADDED T-SLOT SUPPORT FOR ELECTRICAL SHELF; WROCKLAGE; NOTES:; 125 3. ON ALL; ITEM OR FIND NO.; QTY. REQ'D; CAGE CODE; DRAWING OR SPECIFICATION NO.; PART OR; IDENTIFICATION NUMBER; NOMENCLATURE OR DESCRIPTION; NOTES OR REMARKS; PARTS LIST; 34in T-Slot Beam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

1. APPLICABLE STANDARDS / SPECIFICATIONS:

INTERPRET DRAWING IAW ASME Y14.100-2017.

2. REMOVE ALL BURRS AND SHARP EDGES: .010 MIN - .020 MAX.

UNLESS OTHERWISE SPECIFIED, SURFACE ROUGHNESS
MACHINED SURFACES.

THIS DRAWING IS FOR PRELIMINARY
RELEASE ONLY. NOT TO BE CONSIDERED
AS A FINAL PRODUCT.

CAD MAINTAINED. CHANGES SHALL BE
INCORPORATED BY THE DESIGN ACTIVITY.

PROPRIETARY AND CONFIDENTIAL:
THE INFORMATION CONTAINED IN THIS
DRAWING IS THE SOLE PROPERTY OF PURDUE
UNIVERSITY, PURDUE POLYTECHNIC NEW
ALBANY. ANY REPRODUCTION IN PART OR AS
A WHOLE WITHOUT THE WRITTEN PERMISSION
OF PURDUE UNIVERSITY, PURDUE
POLYTECHNIC NEW ALBANY IS PROHIBITED.

UNLESS OTHERWISE SPECIFIED DIMENSIONS ARE IN INCHES TOLERANCES ON ANGLE 1 1 PLACE DECIMAL .1 2 PLACE DECIMAL .02 3 PLACE DECIMAL .005 | FILENAME: Full Drawings.SLDDRW | PURDUE POLYTECHNIC NEW ALBANY 3000 TECHNOLOGY AVE NEW ALBANY, IN 47150

PREPARED | R. REYNOLDS | 2/9/2022

TITLE
TEAM 3 TOP ASSEMBLY

THIRD ANGLE PROJECTION | CHECKED M. WROCKLAGE | | 2/9/2022

ENGINEER M. WROCKLAGE | | 2/9/2022

SIZE D 6D418 | CAGE CODE | DWG NO. 2000

APPLICATION | | | SCALE: 1:1 | SHEET 1 OF 37

8 | 7 | 6 | 5 | 4 | 3 | 1

D

REVISIONS

REV | DESCRIPTION | DATE | APPROVED
00 | PRELIMINARY RELEASE | 2/9/2022 | M. FETTIG
01 | UPDATED APPLICATION AND DRAWING NO. | 3/24/2022 | M. WROCKLAGE

1. APPLICABLE STANDARDS / SPECIFICATIONS:

INTERPRET DRAWING IAW ASME Y14.100-2017.

2. REMOVE ALL BURRS AND SHARP EDGES: .010 MIN - .020 MAX.
UNLESS OTHERWISE SPECIFIED, SURFACE ROUGHNESS

4. MATERIAL: HDPE PLASTIC.

THIS DRAWING IS FOR PRELIMINARY
RELEASE ONLY. NOT TO BE CONSIDERED
AS A FINAL PRODUCT.

CAD MAINTAINED. CHANGES SHALL BE
INCORPORATED BY THE DESIGN ACTIVITY.

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

PURDUE POLYTECHNIC NEW ALBANY
3000 TECHNOLOGY AVE
NEW ALBANY, IN 47150
BOTTOM FRONT PANEL

Full Drawings.SLDDRW

PREPARED | R. REYNOLDS | 2/9/2022

THIRD ANGLE PROJECTION | CHECKED M. WROCKLAGE 2/9/2022

ENGINEER M. WROCKLAGE 2/9/2022

2000 TEAM 3 FULL ASSEMBLY

8 | 7 | 6 | 5 | 4 | 3 | 1

D

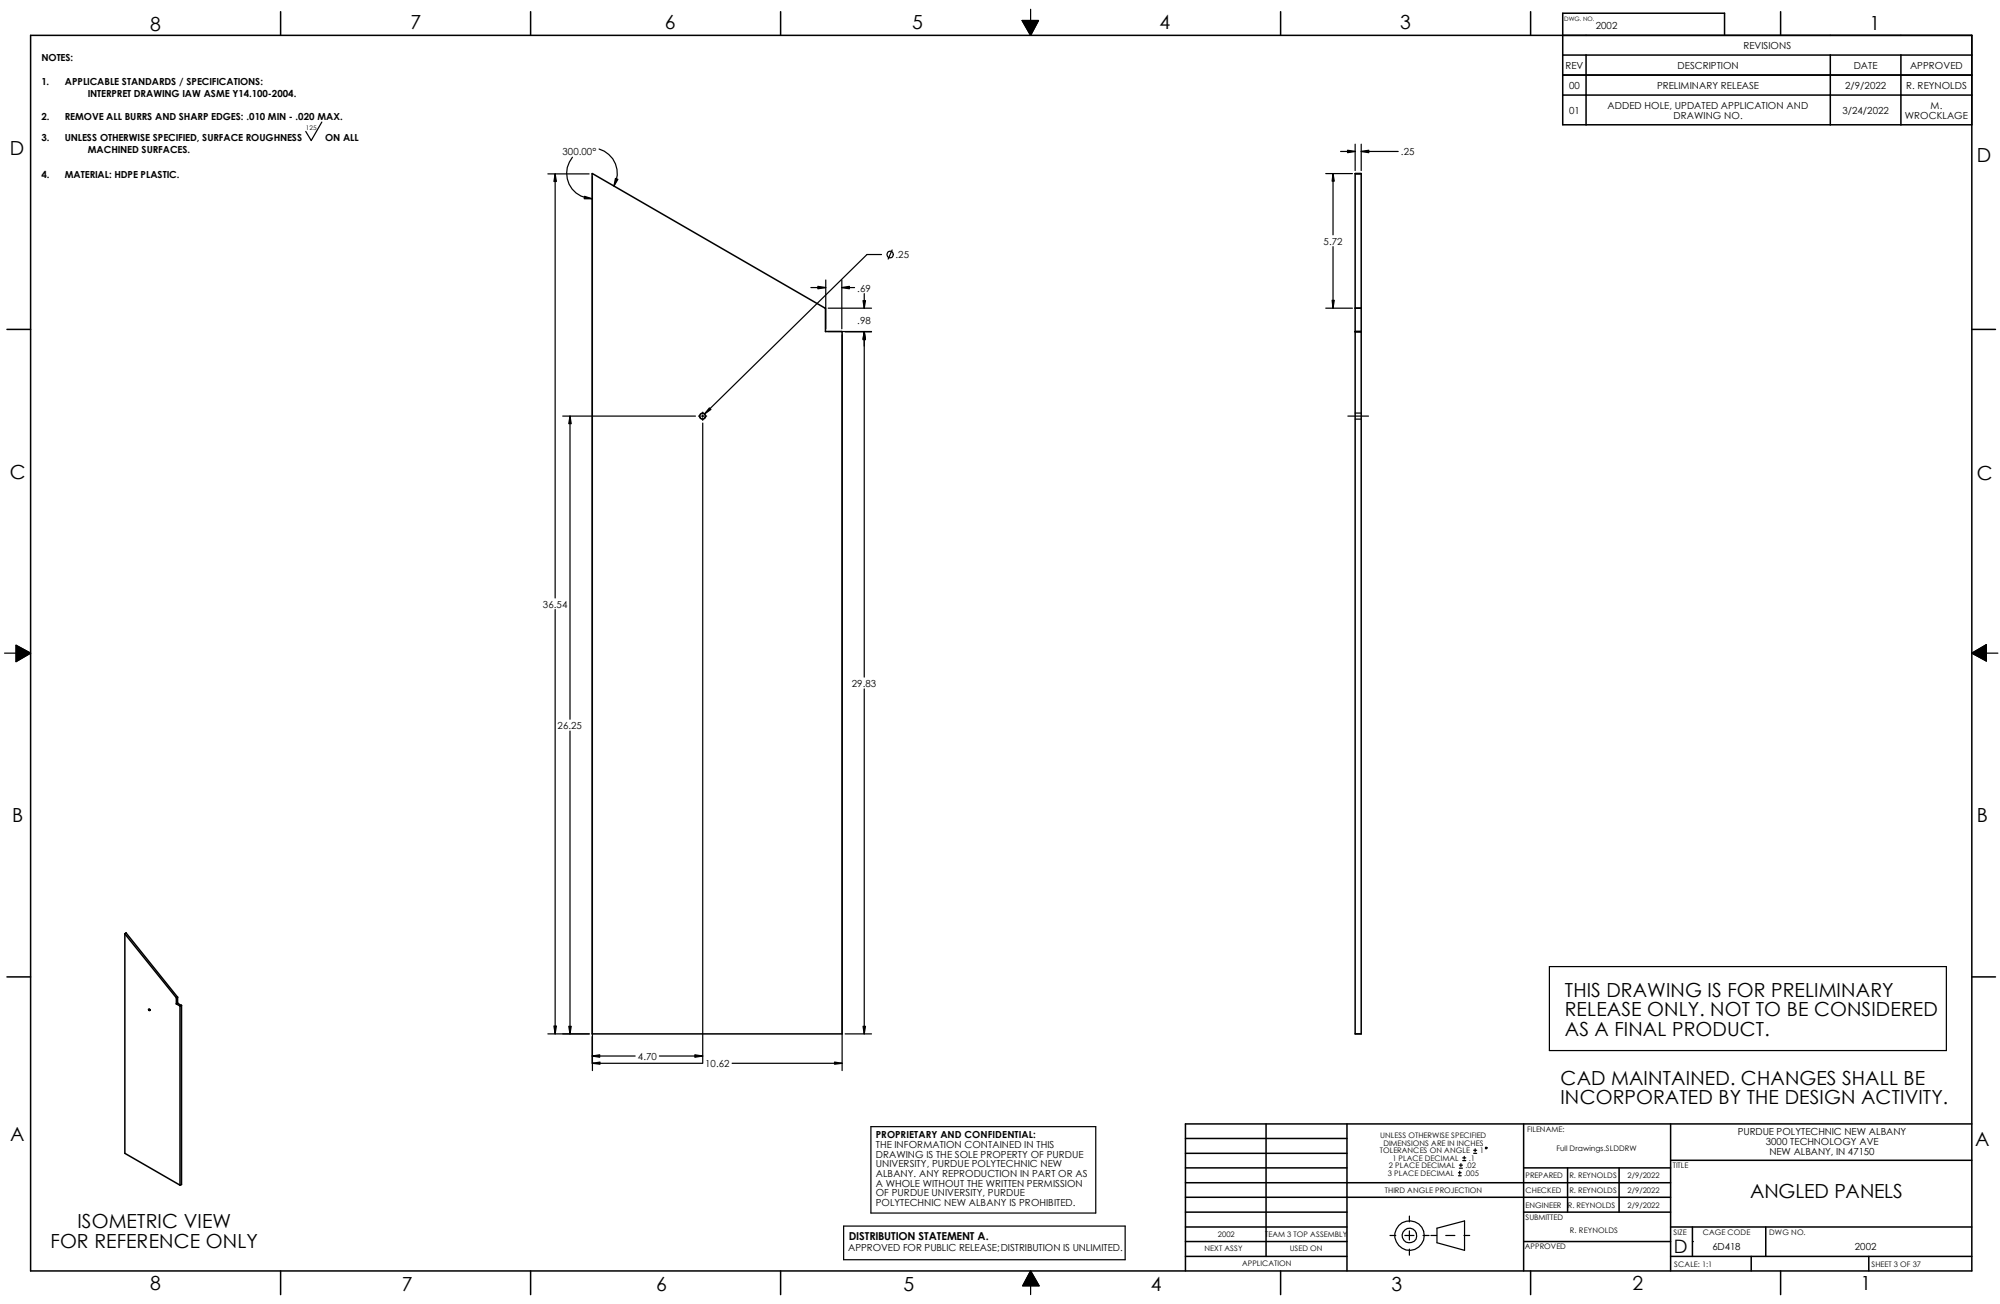
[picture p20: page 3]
ISOMETRIC VIEW; FOR REFERENCE ONLY; APPROVED FOR PUBLIC RELEASE;DISTRIBUTION IS UNLIMITED.; DISTRIBUTION STATEMENT A.; R. REYNOLDS; TITLE; FILENAME:; DWG NO.; DWG. NO.; APPLICATION; NEXT ASSY; USED ON; APPROVED; SUBMITTED; SCALE: 1:1; SHEET 3 OF 37; CAGE CODE; SIZE; NOTES:; 125 3. ON ALL MACHINED SURFACES.

REVISIONS

REV | DESCRIPTION | DATE | APPROVED
00 | PRELIMINARY RELEASE | 2/9/2022 | R. REYNOLDS
01 ADDED HOLE, UPDATED APPLICATION AND | DRAWING NO. | 3/24/2022 | M. WROCKLAGE

1. APPLICABLE STANDARDS / SPECIFICATIONS:

INTERPRET DRAWING IAW ASME Y14.100-2004.

2. REMOVE ALL BURRS AND SHARP EDGES: .010 MIN - .020 MAX.
UNLESS OTHERWISE SPECIFIED, SURFACE ROUGHNESS
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

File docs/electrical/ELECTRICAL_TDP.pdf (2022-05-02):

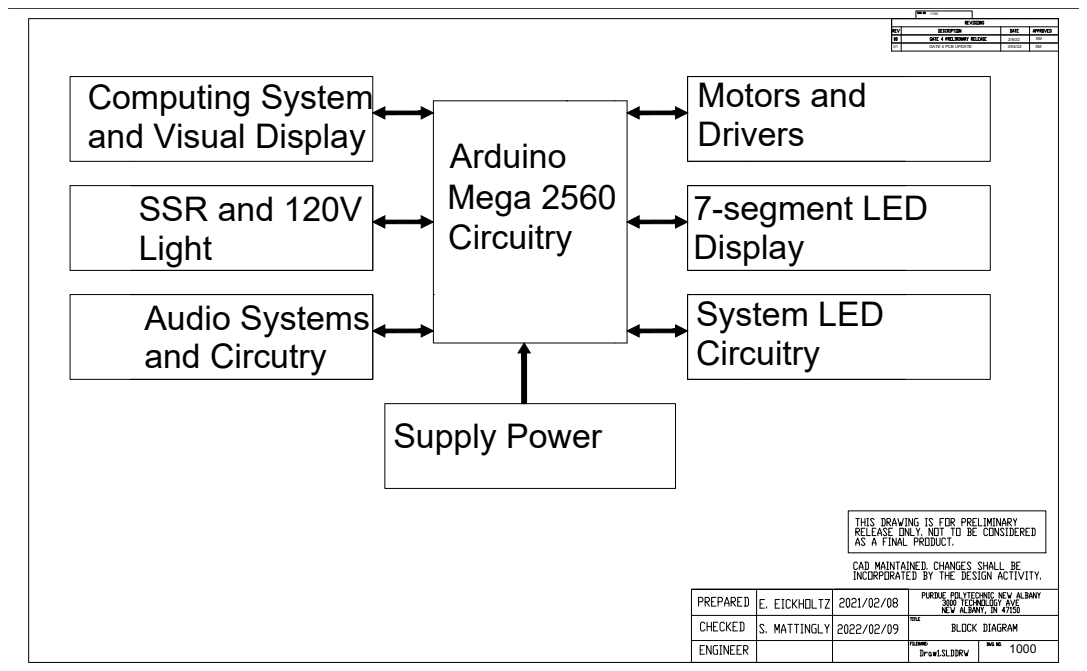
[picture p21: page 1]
GATE 5 PCB UPDATE; Motors and; 7-segment LED; System LED; Audio Systems and Circutry; SSR and 120V; Supply Power; Mega 2560

Computing System
and Visual Display

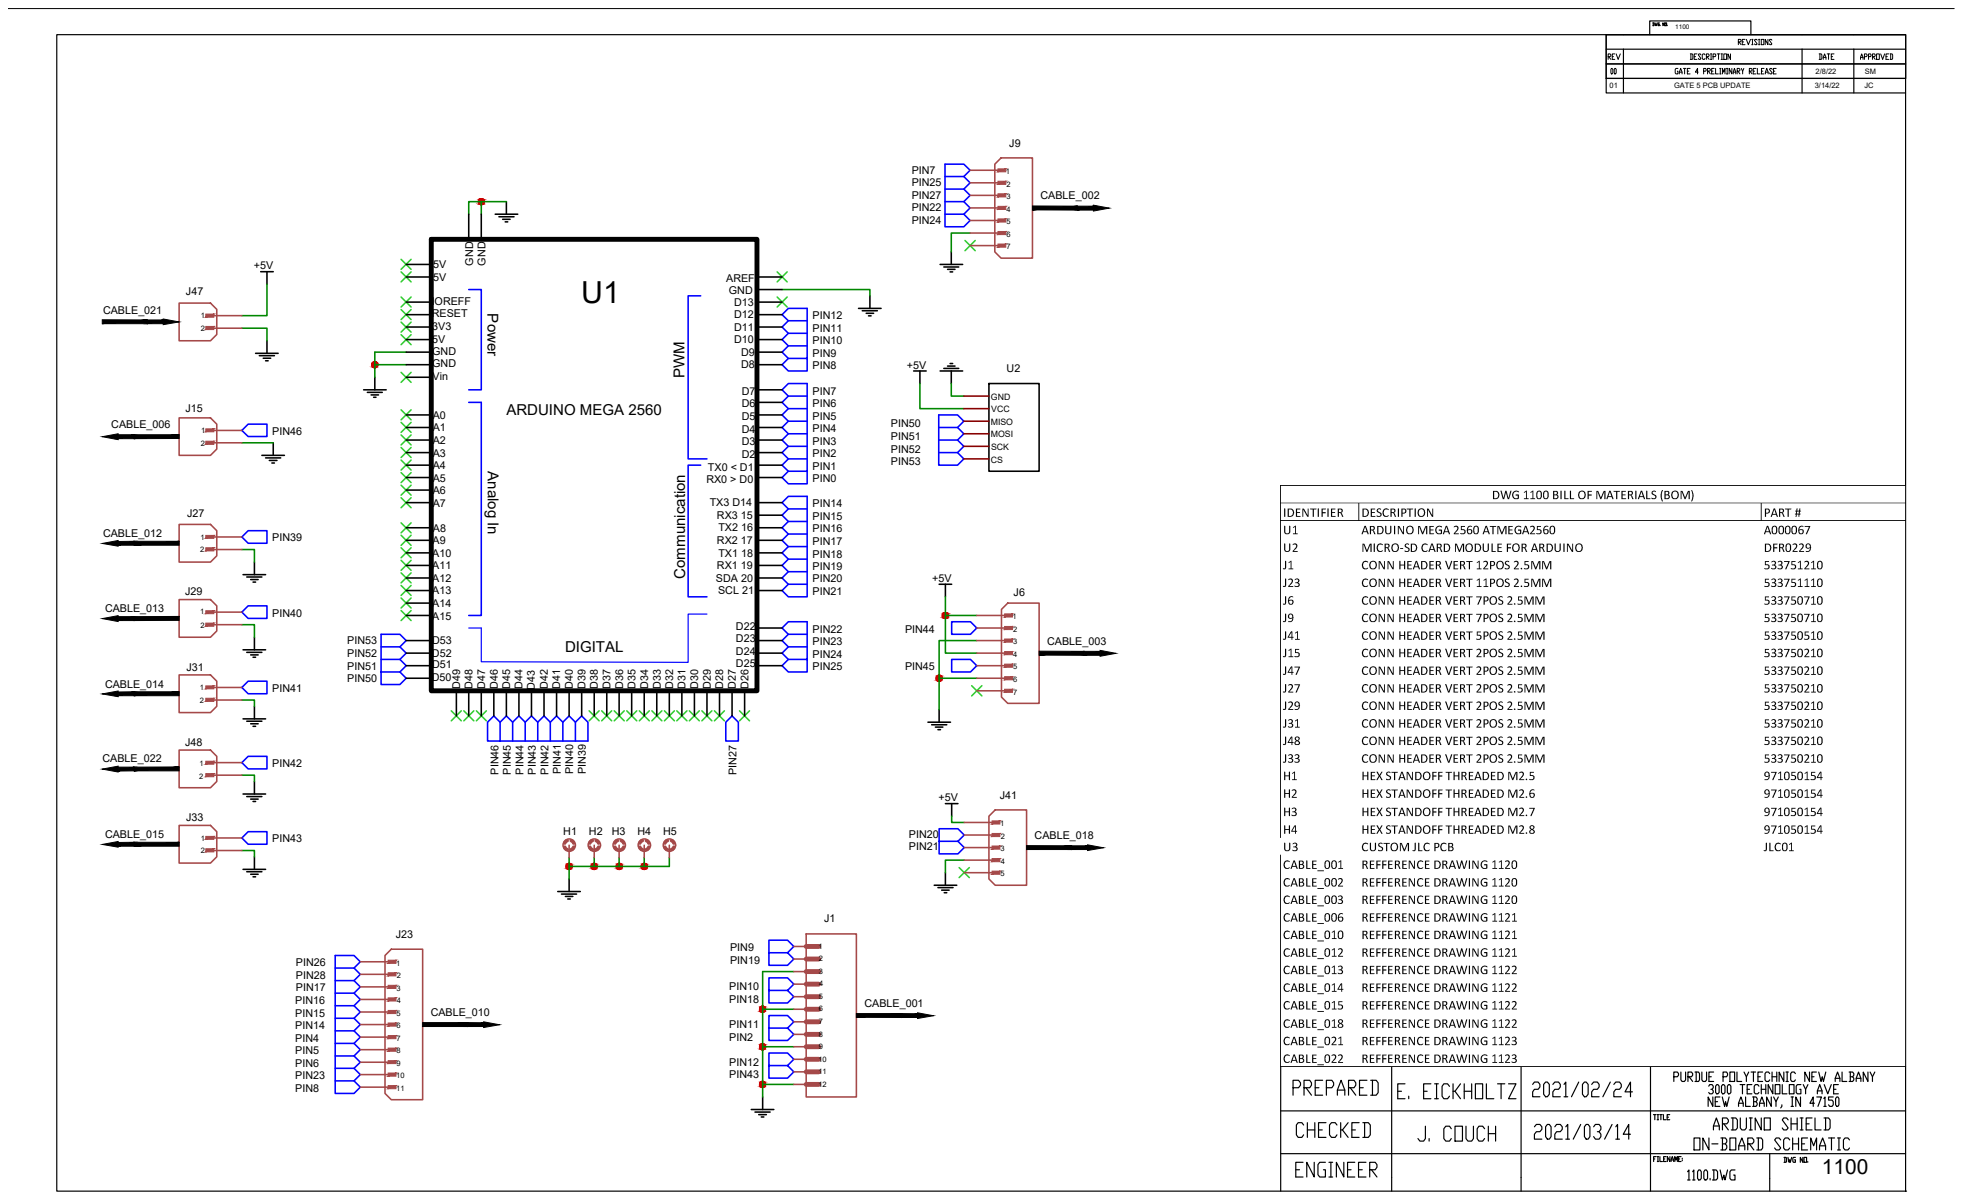
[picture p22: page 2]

VCC MISO MOSI SCK CS

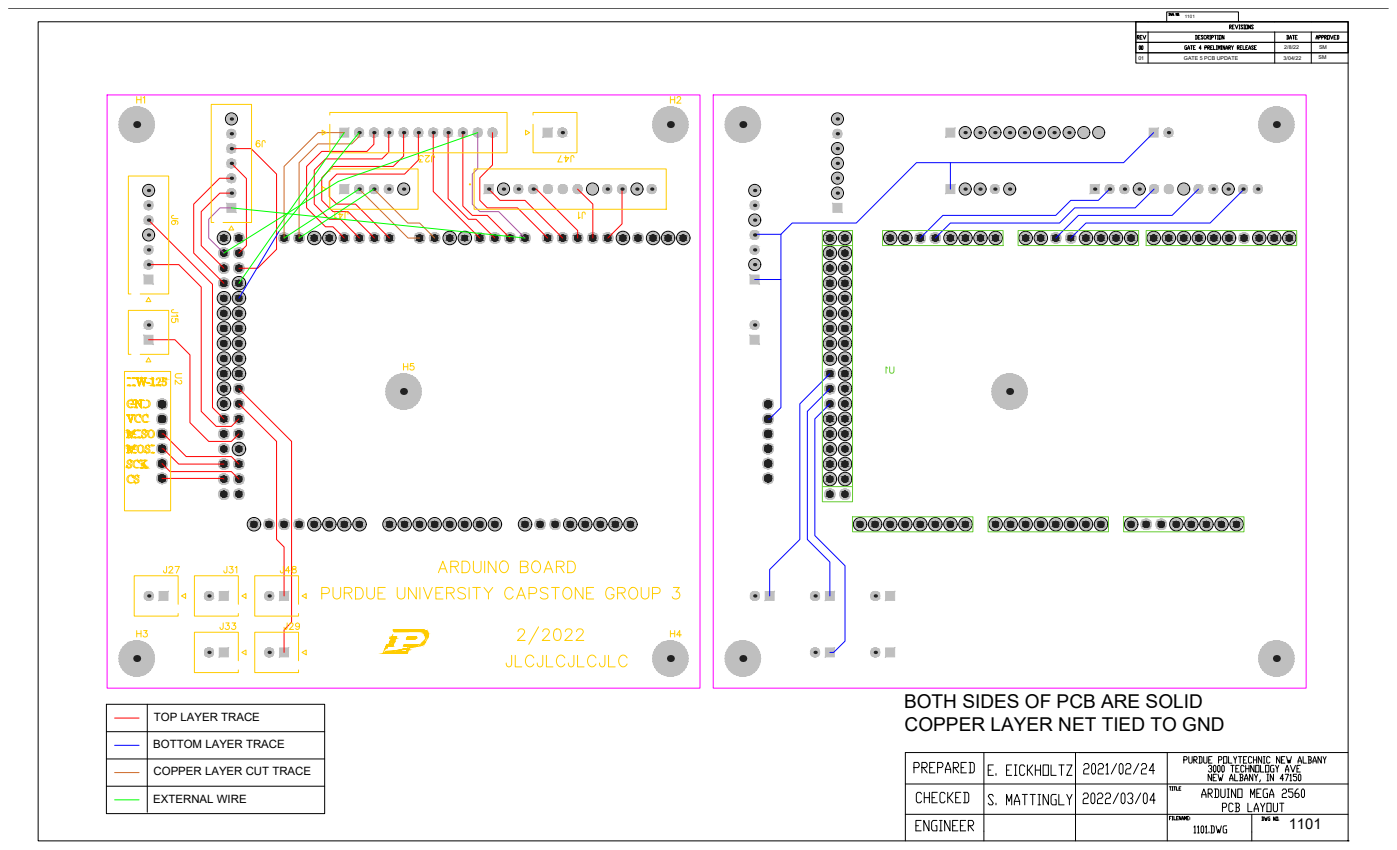
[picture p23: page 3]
GATE 5 PCB UPDATE; EXTERNAL WIRE

BOTH SIDES OF PCB ARE SOLID
COPPER LAYER NET TIED TO GND

TOP LAYER TRACE

BOTTOM LAYER TRACE

COPPER LAYER CUT TRACE

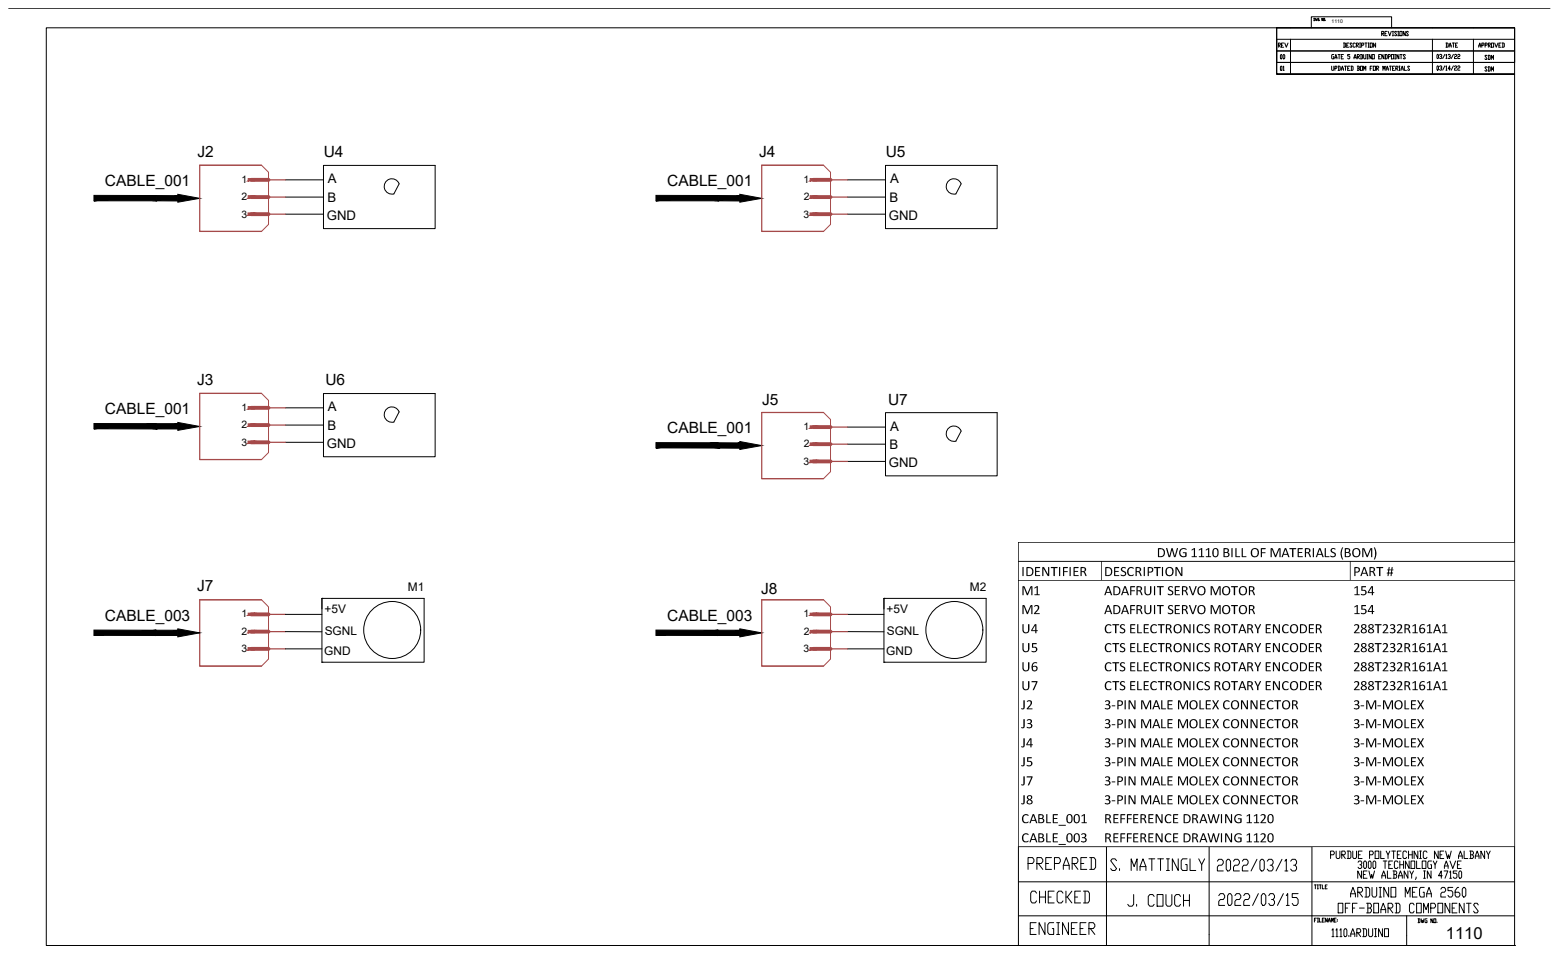
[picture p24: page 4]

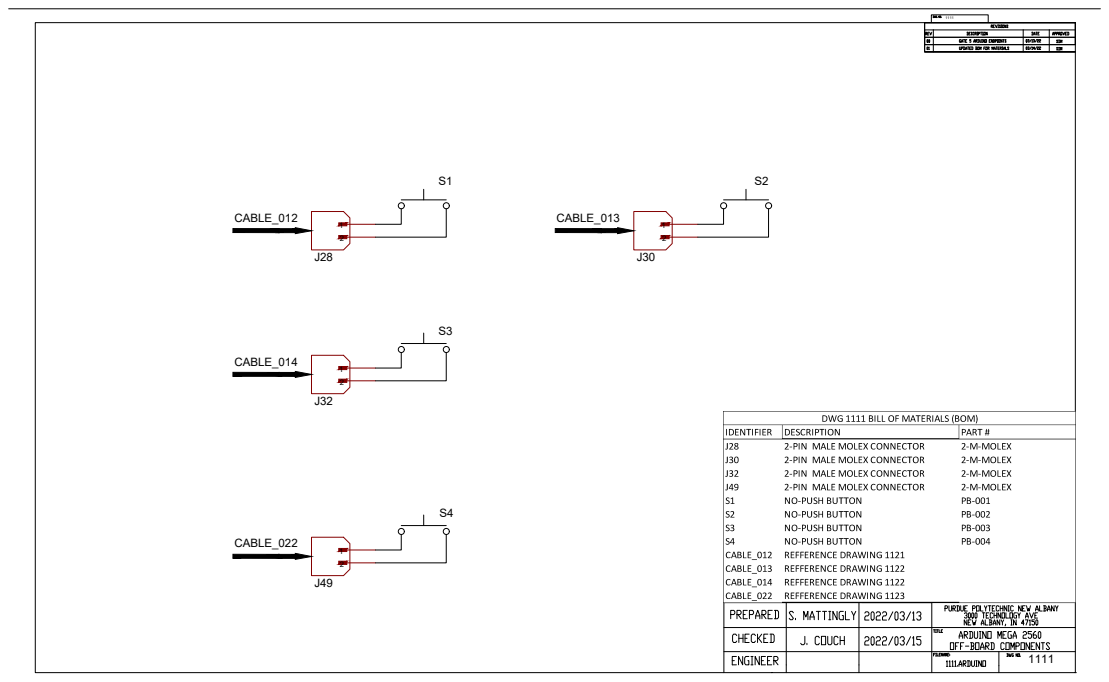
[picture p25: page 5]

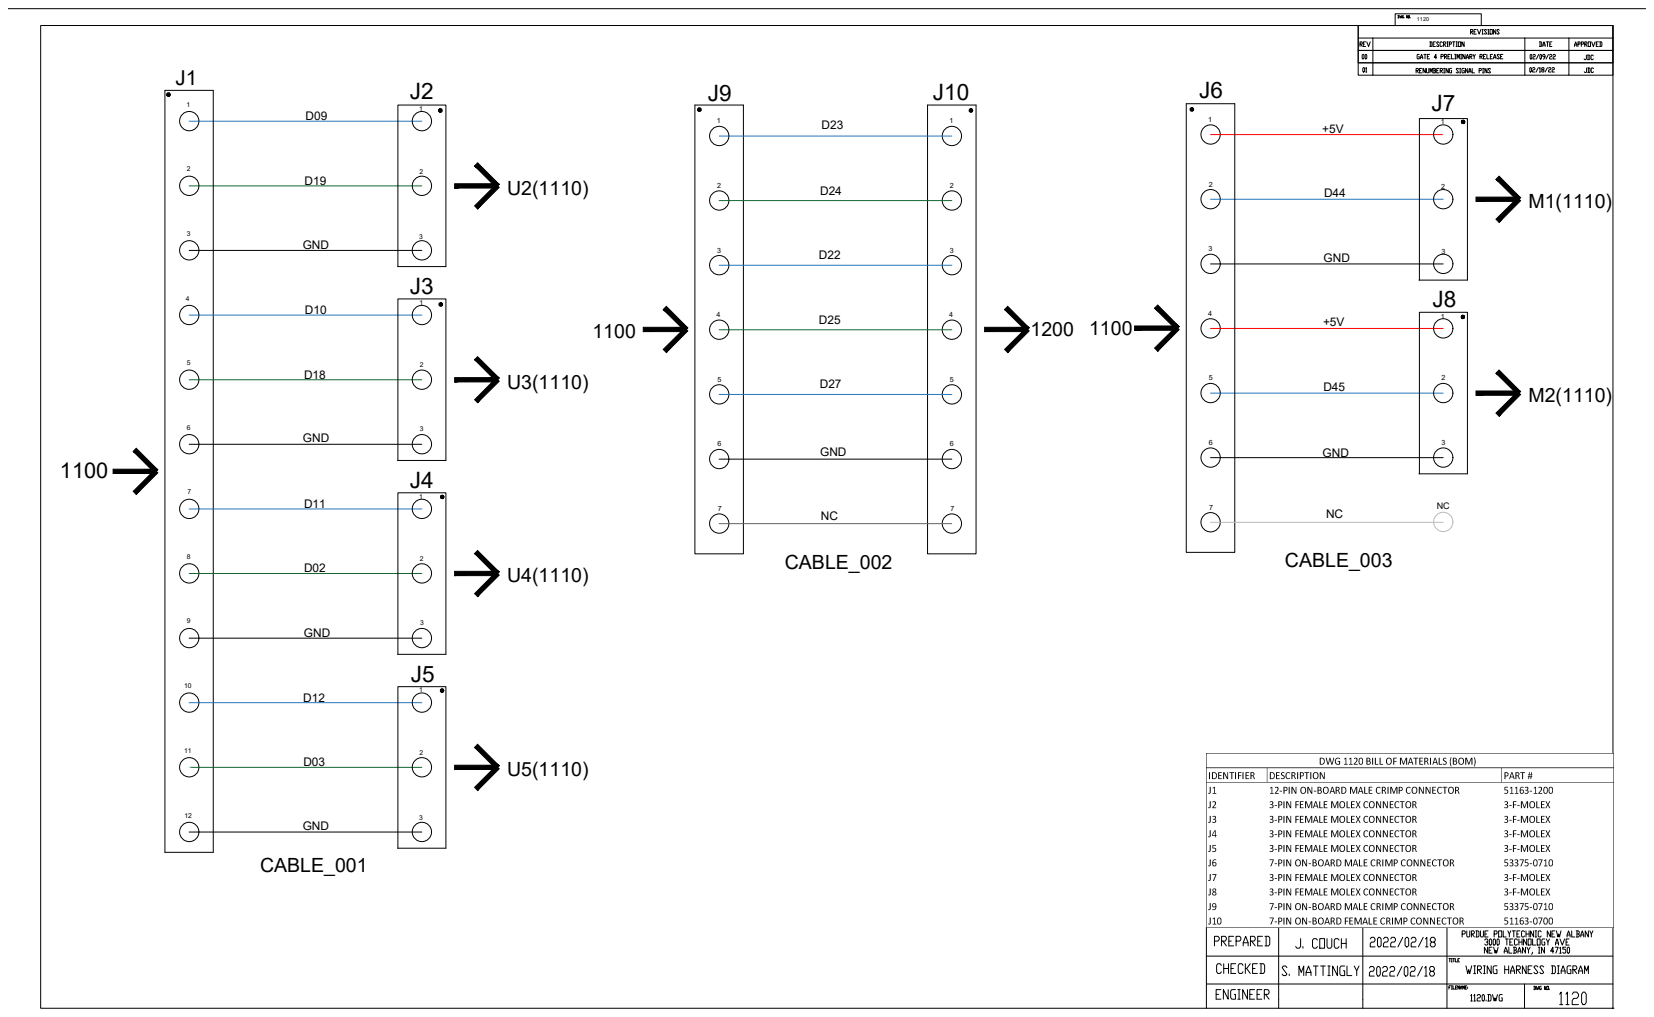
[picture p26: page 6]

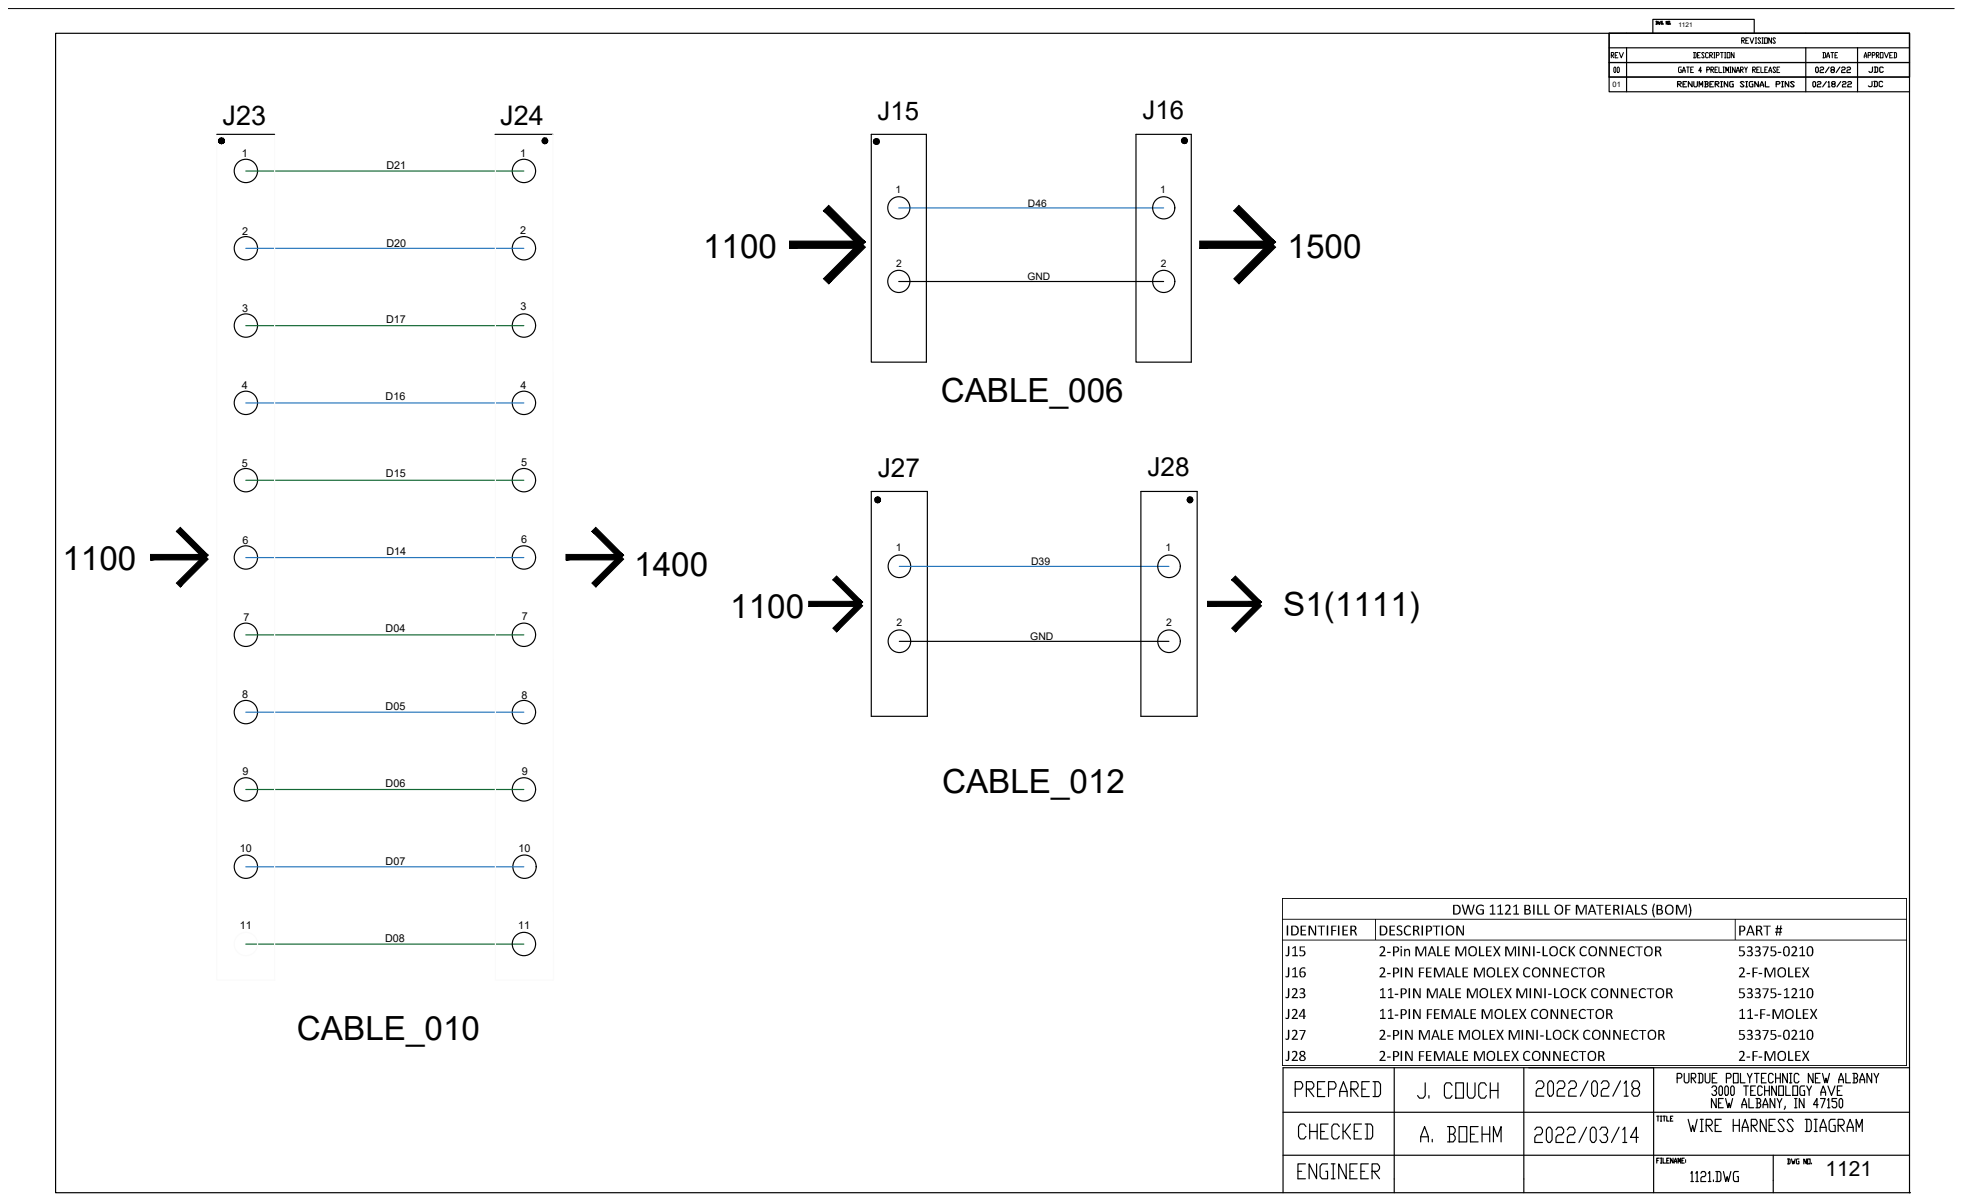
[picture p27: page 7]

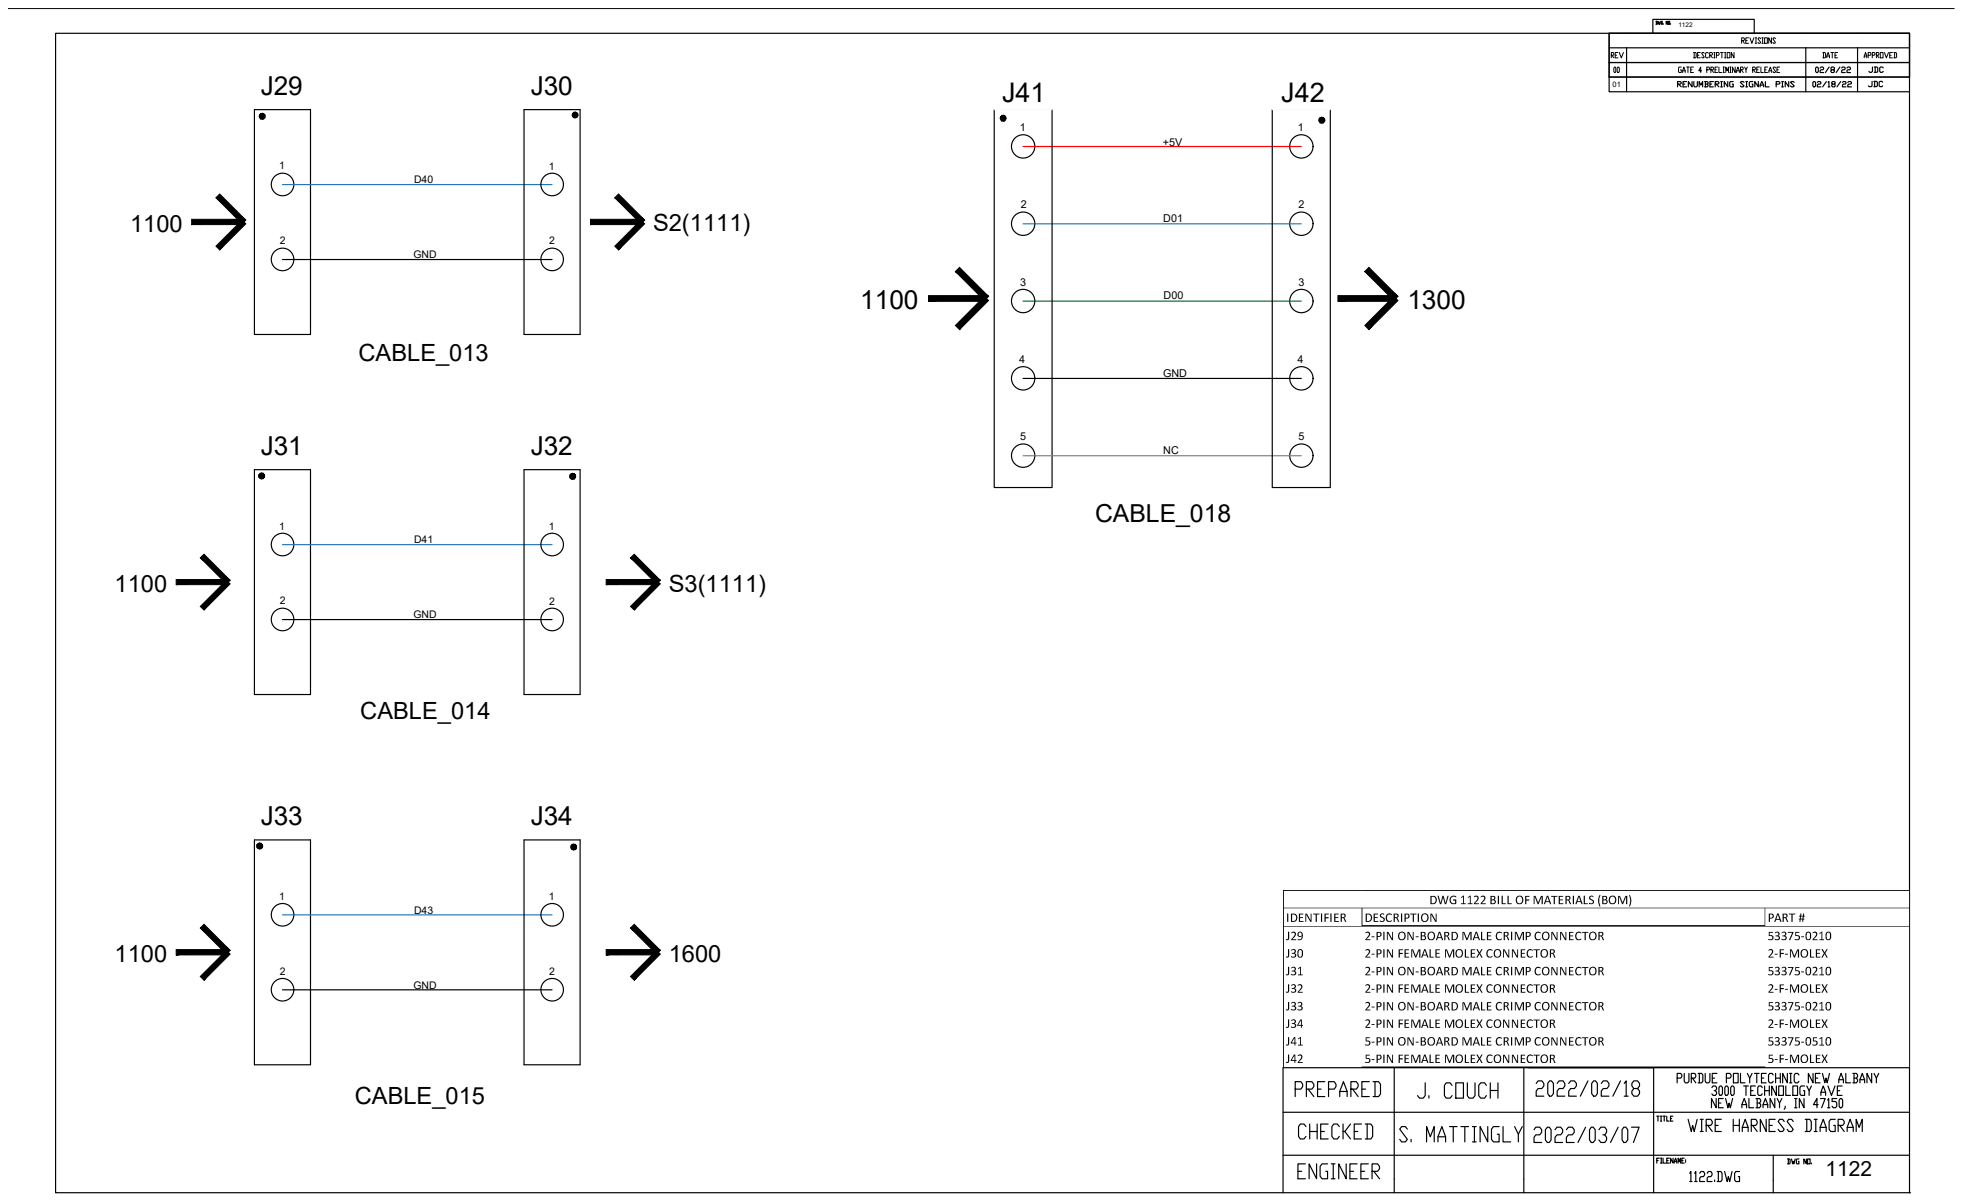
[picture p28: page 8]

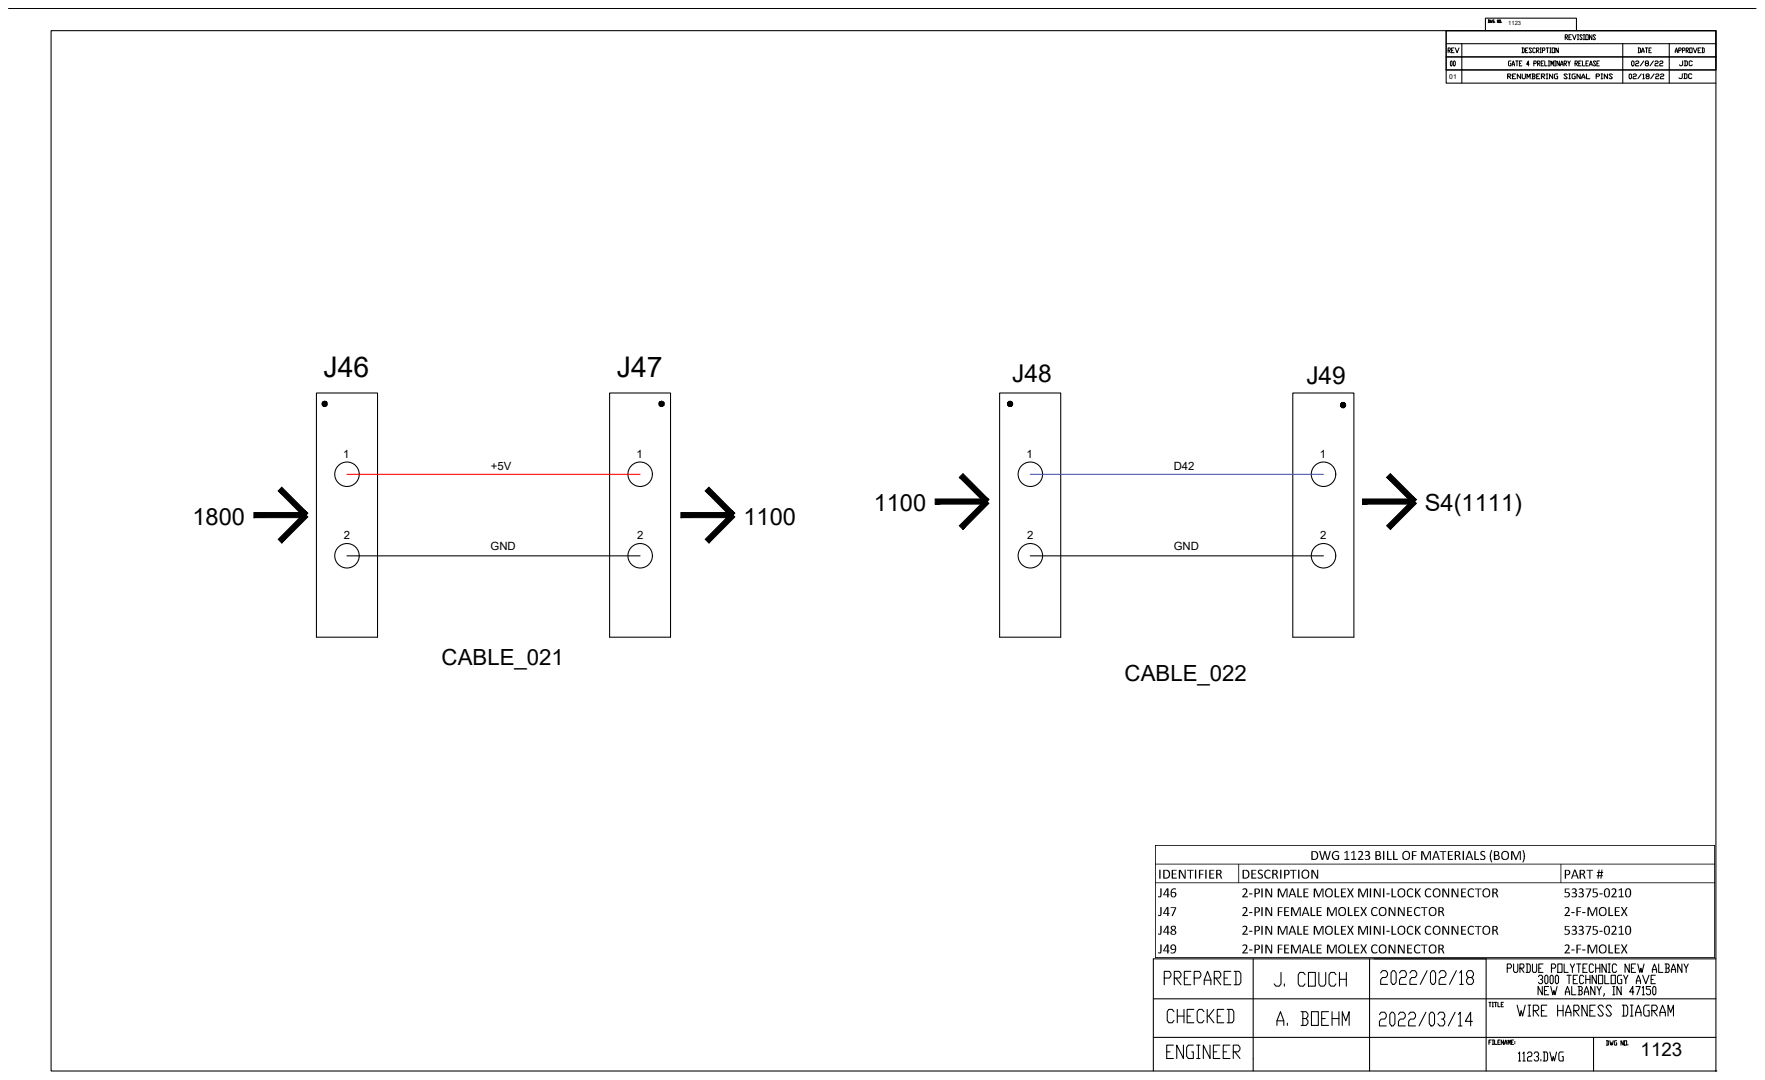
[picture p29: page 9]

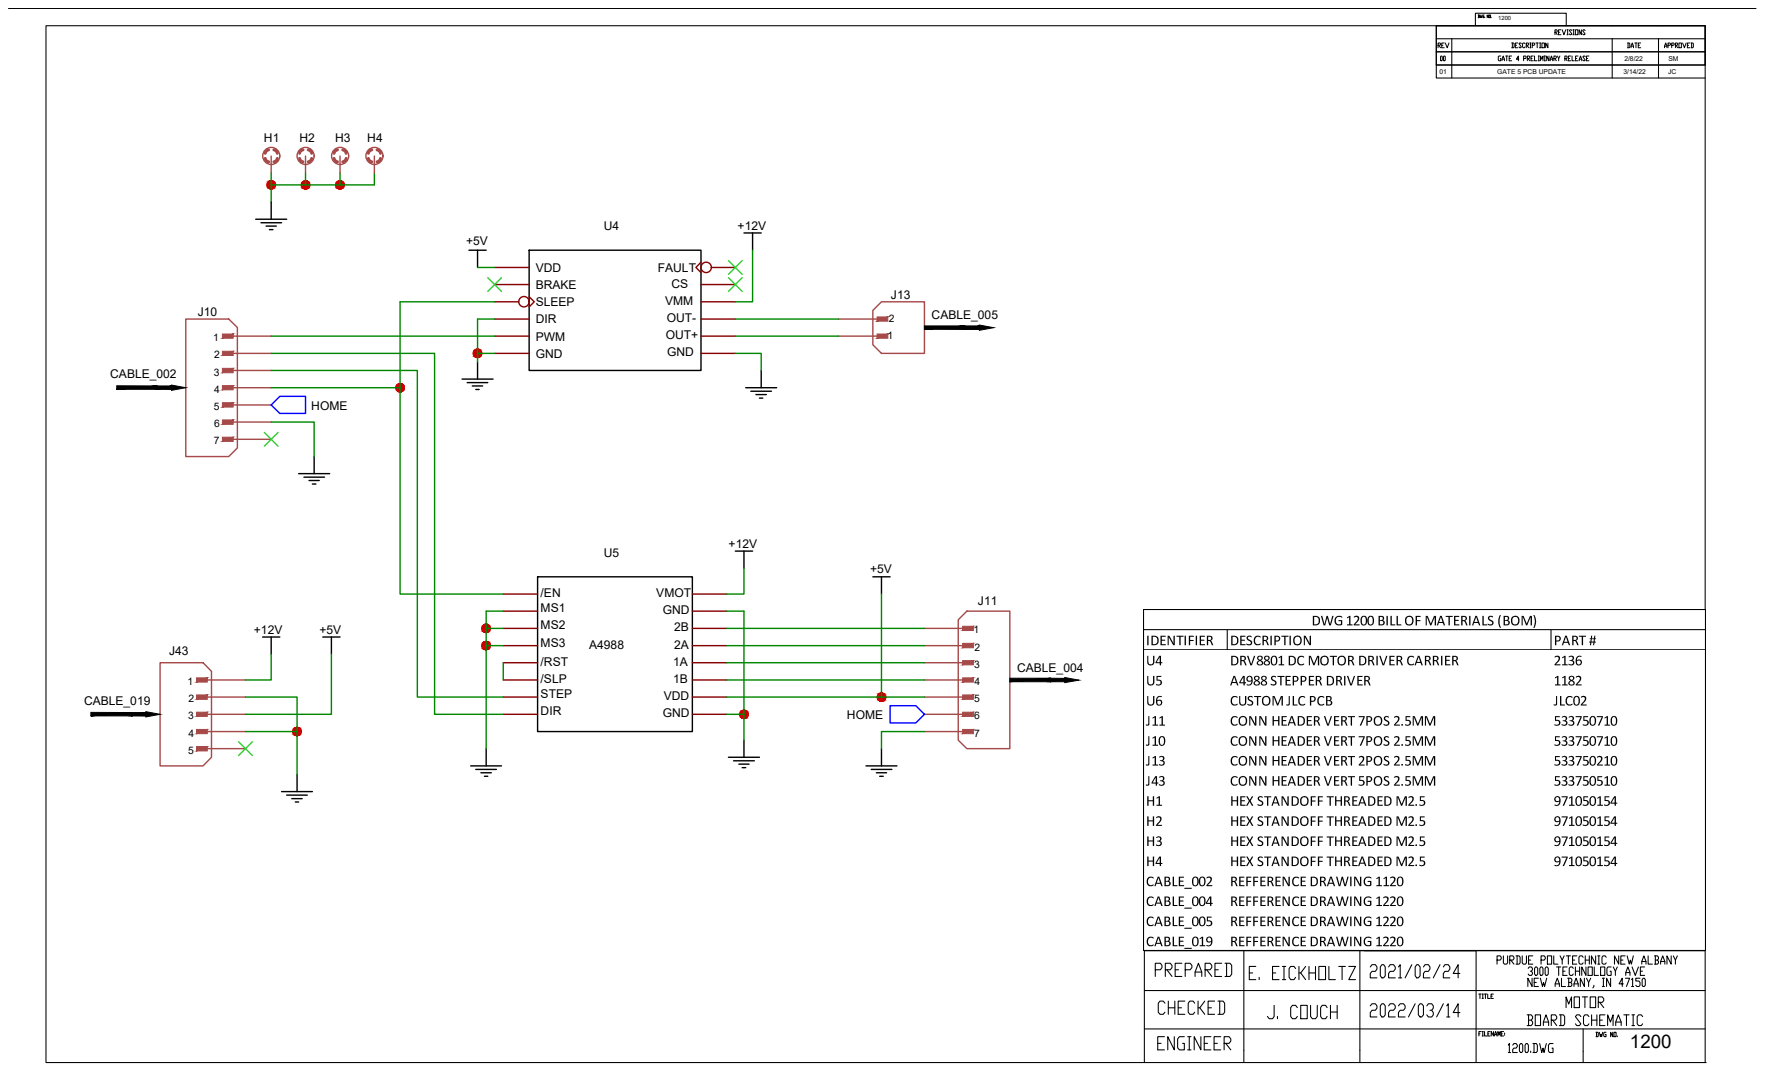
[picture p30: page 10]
GATE 5 PCB UPDATE

GATE 5 PCB UPDATE

BOTH SIDES OF PCB ARE SOLID
COPPER LAYER NET TIED TO GND



ATtiny4313 NC A B G C D EF A B G C D EF A B G C D EF A B G C D EF A B G C D EF A B G C D EF

BOTH SIDES OF PCB ARE SOLID
COPPER LAYER NET TIED TO GND


GATE 5 PCB UPDATE



GATE 5 PCB UPDATE

BOTH SIDES OF PCB ARE SOLID
COPPER LAYER NET TIED TO GND


GATE 5 PCB UPDATE

GATE 5 PCB UPDATE

BOTH SIDES OF PCB ARE SOLID
COPPER LAYER NET TIED TO GND


1800 120VAC


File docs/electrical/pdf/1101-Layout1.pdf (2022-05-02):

EXTERNAL WIRE

01 | GATE 5 PCB UPDATE | 3/04/22 | SM

BOTH SIDES OF PCB ARE SOLID
COPPER LAYER NET TIED TO GND

TOP LAYER TRACE

BOTTOM LAYER TRACE

COPPER LAYER CUT TRACE

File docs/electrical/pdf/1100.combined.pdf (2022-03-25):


01 | GATE 5 PCB UPDATE | 3/14/22 | JC

VCC MISO MOSI SCK CS

EXTERNAL WIRE

01 | GATE 5 PCB UPDATE | 3/04/22 | SM

BOTH SIDES OF PCB ARE SOLID
COPPER LAYER NET TIED TO GND

TOP LAYER TRACE

BOTTOM LAYER TRACE

COPPER LAYER CUT TRACE







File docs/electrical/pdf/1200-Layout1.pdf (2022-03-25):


01 | GATE 5 PCB UPDATE | 3/14/22 | JC

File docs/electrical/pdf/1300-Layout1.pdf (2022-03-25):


ATtiny4313 NC A B G C D EF A B G C D EF A B G C D EF A B G C D EF A B G C D EF A B G C D EF

01 | GATE 5 PCB UPDATE | 3/04/22 | SM

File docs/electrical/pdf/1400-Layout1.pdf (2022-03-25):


01 | GATE 5 PCB UPDATE | 3/04/22 | SM



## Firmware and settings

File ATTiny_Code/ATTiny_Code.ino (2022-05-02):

/*
 * File name:         "ATTiny_Code.ino"
 * Contributor(s):    Elliot Eickholtz
 * Last edit:         3/10/22
 * Code usage:
 * This code is compiled and linked on the Arduino IDE.
 * It is meant to be run on an ATTiny4313 microcontroller, and is intended
 * to control a unique part of an old 7-segment display, which is full of 
 * solely passive components. More information can be found in the project
 * TDP for specific applications.
 * 
 * Full code Repository:
 * https://github.com/Ohm-Slah/Gallagher-Station-Duke-Energy-Museum-Exhibit
 */

//#include <Wire.h>

// Define CPU clockspeed
#define F_CPU 8000000UL

#include <Arduino.h>

#define F_CPU 1000000UL

#define NONE    0b11111111
#define ZERO    0b00000011
#define ONE     0b10011111
#define TWO     0b00100101
#define THREE   0b00001101
#define FOUR    0b10011001
#define FIVE    0b01001001
#define SIX     0b01000001
#define SEVEN   0b00011111
#define EIGHT   0b00000001
#define NINE    0b00011001
#define ZEROP   0b00000010
#define ONEP    0b10011110
#define TWOP    0b00100100
#define THREEP  0b00001100
#define FOURP   0b10011000
#define FIVEP   0b01001000
#define SIXP    0b01000000
#define SEVENP  0b00011110
#define EIGHTP  0b00000000
#define NINEP   0b00011000
#define A       0b00010001
#define C       0b01100011
#define H       0b10010001
#define Z       0b00100101

#define D1 7
#define D2 6
#define D3 5
#define D4 2
#define D5 4
#define D6 3

#define SegA  9
#define SegB 10
#define SegC 11
#define SegD 12
#define SegE 13
#define SegF 14 //14
#define SegG 15
#define DP   16 //16

byte presets[25] = {ZERO, ONE, TWO, THREE, FOUR, FIVE, SIX, SEVEN, EIGHT, NINE, NONE,
                    ZEROP,ONEP,TWOP,THREEP,FOURP,FIVEP,SIXP,SEVENP,EIGHTP,NINEP,
                    A, C, H, Z};

const byte scan[6] = {D1, D2, D3, D4, D5, D6};
const byte segments[8] = {SegA, SegB, SegC, SegD, SegE, SegF, SegG, DP};

char data[6] = {NONE, NONE, NONE, NONE, NONE, NONE};

void setup()  //only runs once at startup.
{
//  Wire.begin(4);                // join i2c bus with address #4
//  Wire.onReceive(receiveEvent); // register event
  Serial.println(9600);
  Serial.setTimeout(5);
  for(int i=2; i<8; i++)
  {
    pinMode(i, OUTPUT);
    digitalWrite(i, LOW);
  }
  
  for(int i=9; i<17; i++)
  {
    pinMode(i, OUTPUT);
    digitalWrite(i, HIGH);
  }
  //delay(1000);
  //digitalWrite(scan[0], HIGH);
  testSegments();
  
}

void loop() { 
  scanAnodes(400);
  //data[0]++;
  getSerial();
  //testSegments();
}

void testSegments()
{
  // sweep trough the annodes with data array 1ms between each
  scanAnodes(300);
  // check serial port for incoming data, replace current data if any
  getSerial();
}

void scanAnodes(uint16_t del)
{
  for(int i=0; i<6; i++)
  {
    for (int j=0; j<8; j++)
    {
      digitalWrite(segments[j], (presets[int(data[i]-'0')])&(0x80>>j));
    }
    digitalWrite(scan[i], HIGH);
    delayMicroseconds(del);
    digitalWrite(scan[i], LOW);
    
  }
}
 
//void receiveEvent(int howMany)
//{
//  int j = 0;
//  
//  while(1 < Wire.available() && j < 6) // loop through all but the last
//  {
//    data[j] = Wire.read(); // receive byte as a character
//    j++;
//  }
//  int x = Wire.read();    // receive byte as an integer
//}

void getSerial()
{
  // checks for serial data at buffer, replaces current data array with new data

  char buff[6];
  
  if(Serial.available())
  {
    //for(int i=0; i<6; i++) data[i] = NONE;
    uint8_t len = Serial.readBytesUntil(0x0A, data, 6);
    //Serial.println(len);

    //for(int i=len; i<6; i++) data[i] = NONE;

    Serial.readBytes(buff, 100);
  }
}

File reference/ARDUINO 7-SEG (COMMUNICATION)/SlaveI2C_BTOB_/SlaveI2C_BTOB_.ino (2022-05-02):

/*
   ya yeet
   This code is for the slave device to receive 'n' bits of data from an i2c bus defined by
   the master device.
   Data requests happen every second and print hello to serial monitor
   see file masterI2C for rest of code
*/

#define F_CPU 8000000 //this is for the attiny 4313

#include <Wire.h>

#include <Arduino.h>

// define bytes for 7-segment display to replace these words
#define NONE  0b11111111
#define ZERO  0b00000011
#define ONE   0b10011111
#define TWO   0b00100101
#define THREE 0b00001101
#define FOUR  0b10011001
#define FIVE  0b01001001
#define SIX   0b01000001
#define SEVEN 0b00011111
#define EIGHT 0b00000001
#define NINE  0b00011001
#define A     0b00010001
#define C     0b01100011
#define H     0b10010001
#define Z     0b00100101

// define I/O pins tied to 7-segment anodes
#define D1 7
#define D2 6
#define D3 5
#define D4 2
#define D5 4
#define D6 3

// define I/O pins tied to 7-segment cathodes
#define SegA  9
#define SegB 10
#define SegC 11
#define SegD 12
#define SegE 13
#define SegF 1  //14
#define SegG 15
#define DP   0  //16

// define array of presets to scroll through
byte presets[15] = {ZERO, ONE, TWO, THREE, FOUR, FIVE, SIX, SEVEN, EIGHT, NINE, NONE, A, C, H, Z};

// define order of annodes tied to their I/O that needs to be multiplexed
const byte scan[6] = {D1, D2, D3, D4, D5, D6};
// define order of segments tied to their I/O
const byte segments[8] = {SegA, SegB, SegC, SegD, SegE, SegF, SegG, DP};

// array to hold data that will be scrolled through to multiplex
char data[6] = {NONE, NONE, NONE, NONE, NONE, NONE};
//char data[6] = {ZERO, ZERO, ZERO, ZERO, ZERO, ZERO};
//char data[6] = {ONE, ONE, ONE, ONE, ONE, ONE};
//char data[6] = {ZERO, TWO, FOUR, ONE, ONE, ONE};

void setup()
{
   Wire.begin(8);                // join i2c bus with address #8
   Wire.onReceive(receiveEvent); // register event
   Serial.begin(9600);           // starts serial output

    for(int i=3; i<8; i++)
    {
      pinMode(i, OUTPUT);
      digitalWrite(i, LOW);
    }
    
    for(int i=9; i<16; i++)
    {
      pinMode(i, OUTPUT);
      digitalWrite(i, HIGH);
    }
    pinMode(0, OUTPUT);
    digitalWrite(0, HIGH);
    pinMode(1, OUTPUT);
    digitalWrite(1, HIGH);
  
}

void loop()
{
   scanAnodes(300);
}

void scanAnodes(uint16_t del)
{
  // push currently saved data onto the 7-segment LEDs, multiplexing them once
 
  for(uint8_t i=0; i<6; i++)
  {
    for (uint8_t j=0; j<8; j++)
    {
      
      digitalWrite(segments[j], (presets[data[i]]) & (0x80 << j));
     
    }
    
    //on and off anodes segments 
    digitalWrite(scan[i], HIGH);
    delayMicroseconds(del);
    digitalWrite(scan[i], LOW);
    
  }
}

// function that executes whenever data is requested by master
// this function is registered as an event, see setup()

void receiveEvent(int howMany) //contains the amount of bytes
{
  int count = 0;

  while(1 < Wire.available())
  {
    byte c = Wire.read(); //grabs a byte at a time 
    data[count] = c; 
    count++; 
    if (count > 5)
    {
      break; 
    }
  }
  for(; count<6; count++)
  {
   
    data[count] = TWO;
  }
}

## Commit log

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2021-11-19 Revert "Update phases.h"
    This reverts commit 8b30d877e411545e9f12309b7990bc96a496622e.
    [phases.h]
2021-11-19 Revert "Update phases.h"
    This reverts commit 4a9e4769eced52ef17f41c931c48aabdffabc4e4.
    [phases.h]
2021-11-19 Revert "Update phases.h"
    This reverts commit 27b599176f2c09088dffceef257543cc201359a3.
    [phases.h]
2021-11-19 Revert "Update phases.h"
    This reverts commit 695fabe965835ce643aa47b955647cab7f52dcab.
    [phases.h]
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2021-11-22 Add LED's (#27)
    * Add files via upload
    * Minor Tweaks
    * Update main.ino
    Fixes #8
    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
    [main.ino, phases.cpp, phases.h]
2021-11-22 Servo (#20)
    * Create Servo
    This is the code for the Servo motor, in this code the servo will turn from zero degrees to 270 degrees back to zero degrees.
    * Delete Servo
    Changed to servo (had stepper and servo mixed up)
    * Cleanup
    Fixes #20
    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
    [phases.cpp, phases.h]
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2021-11-24 Buttons/switches (#30)
    * Fixed Servo issues
    * Added buttons and interrupts
    Fixes #5
    [main.ino, phases.cpp, phases.h]
2021-11-29 Arduino audio (#28)
    * Delete arduino_sd.ino
    changed code to what i got working previously
    Fixes #16
    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
    [phases.cpp, phases.h]
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2022-01-23 Rewrite led blinking (#54)
    * Adding Link library bc I'm lazy
    * Added led states for different phases
    * Deep sleep (#55)
    * added deep sleep and cleaned phase zero
    * Updated sleep timing to 3 hours
    * fixed errors
    [main.cpp, phases.cpp, phases.h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]
2022-01-29 Rewrite led blinking (#58)
    * Redo pinout, add blink() where needed
    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
    [main.cpp, phases.cpp, phases.h]
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2022-02-18 Added Drawings (#61)
    * Create docs
    * Delete docs
    * Create docs
    * Delete 1300.SEGMENT.dwg
    * Create pdf
    * Delete pdf
    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
    [1300.SEGMENT.dwg]
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2022-02-21 zoomed drawing to fit
    [1300.SEGMENT.dwg]
2022-02-21 Added Wire Harness Diagram Folder
    All wire harness diagrams that Jackson did are here, need editing
    [1110_DWG.dwg, 1120_DWG.dwg, 1130_DWG.dwg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]
2022-02-21 Added "POWER BUS" to 1300
    [1130_DWG.dwg, 1140_DWG.dwg]
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2022-02-21 Updated J-connector names
    Names now match the 1100 arduino schematic
    [1110_DWG.dwg, 1120_DWG.dwg, 1130_DWG.dwg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]
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2022-02-22 add current versions of what Elliot has
    [1100.dwg, 1110.dwg, 1200.dwg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]
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2022-02-23 BOM J connector name space
    Removed spaces in BOM because it annoying
    [1100.dwg, BOM_OLE.xlsx]
2022-02-23 Added LEDS 2-pin connectors
    DWG files (1200 and 1190) these need to be checked off
    [1190_DWG.dwg, 1200_DWG.dwg]
2022-02-23 BOM of all Wiring Harness
    This contains all BOM for the wiring harness diagram
    [Wiring Harness(BOM).xlsx]
2022-02-24 Cleaned up duplicate files, reformatted dwg's
    I converted all dwg electrical drawings to the 2013 version in order to work on this on my downtime at work.
    [1100.dwg, 1110.dwg, 1110_DWG.dwg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]
2022-02-24 update drawings to new standards
    update 1100, 1110, 1200, 1210, 1300, 1310, 1400, 1410.
    Create files for other drawings
    [1100.dwg, 1110.dwg, 1200.dwg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]
2022-02-24 Updated BOM and drawings
    updating drawings to new standards, as well as adding PCB stuff.
    [1500.dwg, 1510.dwg, 1600.dwg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]
2022-02-24 Final inspection before review submittal
    [1100.dwg, 1200.dwg, 1210.dwg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]
2022-02-26 Overall editing of schematics and wire harnesses
    changes are NOT DONE. Do not edit without notifying Samuel
    [1100.dwg, 1110.dwg, 1110_DWG.dwg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]
2022-02-26 Added cables and edited connectors
    Connectors now reflect what is on PCB accurately. Not finished
    [1100.dwg, 1170_DWG.dwg, 1200.dwg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]
2022-02-28 Drawings updated
    Specifically updated BOM on 1100.
    [1100.dwg, 1110.dwg, 1110_DWG.dwg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]
2022-03-05 Revisions for main drawings
    Summary:
    -updated numbers to reflect current scheme. (1110 -> 1101, 1210 -> 1201, etc.)
    -updated BOM in all drawings to correctly refference drawing numbers
    whats needed:
    -off-board components finished
    -re-order connectors relative to schematics
    -fill in on schematics
    [1100.dwg, 1101.ARDUINO.dwg, 1110.dwg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]
2022-03-05 Resized windows
    no major edits, couple text fixes
    [1100.dwg, 1101.ARDUINO.dwg, 1200.dwg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]
2022-03-06 CAD design for Fuses
    This file contains the schematic for the fuses for the electric design. These values have been calculated for and should be the correct values.
    [Fuses.dwg]
2022-03-06 Fuses fitting template
    Updated Fuses DWG to fit template
    [Fuses.dwg]
2022-03-06 Updated fuse diagram.
    Edited BOM
    [Fuses.dwg]
2022-03-07 SCHEMATIC OVERHAUL
    Following changes were made:
    - Cable refferences were updated on schematics
    -Connectors were moved to the new numbering scheme
    -Connectors going between boards (A cable going from the arduino board to the motor board for example) are only placed ONCE and always refference the original drawing (that same cable may show twice,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
    -drawings are now in order
    -endpoints just need to be added, some schematics will be updated as new endpoints have new names
    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
    [1100.dwg, 1101.ARDUINO.dwg, 1110_DWG.dwg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]
2022-03-10 Reorganized Files, Renamed, and Reformatted DWG's
    [1100.dwg, 1101.ARDUINO.dwg, 1120.dwg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]
2022-03-10 First attempt at pdf generation
    [Fuses.dwg]
2022-03-10 Updated 1400 to match As-Built
    [1400.dwg, BOM_OLE.xlsx]
2022-03-10 OVERKILL, PURGE, EXPLODE, and rename all drawings
    [1100.dwg, 1101.ARDUINO.dwg, 1120.dwg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]
2022-03-13 Created 1210
    This contains new end point connectors for DC motor and Stepper Motor
    [1210.dwg]
2022-03-13 Added BOM for parts on 1110-1111
    end points for 1100 arduino board added
    [1110.ARDUINO.dwg, 1111.ARDUINO.dwg, BOM_PARTS.xlsx]
2022-03-13 added 1610, added BOM from sam and jackson
    [1610.SSR.dwg, BOM(from jackson).xlsx, BOM(from sam).xlsx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]
2022-03-13 Created 1510
    In this drawling endpoint speaker endpoint connectors were made
    [1510.dwg]
2022-03-14 Merged BOM, updated BOM on a few drawings, editing 1800 for final print.
    1800 isnt done yet, need to think about how it is being executed before finishing
    [1110.ARDUINO.dwg, 1111.ARDUINO.dwg, 1210.dwg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]
2022-03-14 Updated 1100
    Changed BOM (Cap)
    fixed formatting issues
    lines were in the wrong direction for connectors
    [1100.dwg]
2022-03-14 Update 1111.ARDUINO.dwg
    Capitolized BOM
    [1111.ARDUINO.dwg]
2022-03-14 Fixed some details in1121
    standardized font size
    all caps
    [1121.dwg, BOM_OLE.xlsx]
2022-03-14 (DWG 1100, DWG 1110, Sam's BOM)
    1100 changed back orientation of cable to the right facing.
    capatilized BOM of (Sam's BOM) & 1110
    Fixed color for connectors of DWG 1100 & 1110
    [1100.dwg, 1110.ARDUINO.dwg, BOM(from sam).xlsx]
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2022-03-14 Fixed orientation indicator & CAPS
    FIXED BOM FORMATTING AND
    ORIENTATION INDICATOR OF WIRING HARNESS
    [1120.dwg]
2022-03-14 FIXED DWG 1200 FORMATTING
    REMOVED OUTSIDE NUMBERING (UNECESSARY)
    MADE EVERTHING THE SAME SIZE FONT
    CAP THE BOM
    [1200.dwg]
2022-03-14 RECONNECTED LINES (DWG 1201)
    RECONNECTED LINES
    PURDUE LOGO STILL NEEDS TO FIXED
    [1201.dwg]
2022-03-14 FIXED BOM CAP (DWG 1210)
    FIXING BOM WITH CAPS (FORMATTING)
    [1210.dwg]
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2022-03-15 SCHEMATIC ISSUE & FORMATTED BOM
    FIXED SCHEMATIC ISSUE SPLIT APART END POINT CONNECTORS
    [1210.dwg]
2022-03-15 UPDATE
    did not change anything
    [1210.dwg]
2022-03-15 UPDATE
    orientation dots changed and as well as end schematic numbers changed from 1200 to 1210.
    [1220.dwg]
2022-03-15 Zoomed on drawings and finished 1800
    1800 needs reviewed, that is all
    [1120.dwg, 1121.dwg, 1122.dwg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]
2022-03-15 Reformatted BOM, deleted old ones
    [BOM(from jackson).xlsx, BOM(from sam).xlsx, BOM_OLE.xlsx]
2022-03-15 UPDATED ALL BOM AND CONNECTORS
    Edits to some readability and cosmetic consistencies
    [1100.dwg, 1101.dwg, 1110.ARDUINO.dwg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]
2022-03-15 Finalized formatting for 1100 series drawings
    final edits in readability and aesthetics
    [1100.dwg, 1101.dwg, 1110.dwg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]
2022-03-15 finalized 1200 series drawings
    [1200.dwg, 1201.dwg, 1210.dwg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]
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2022-03-16 finalize drawlings
    1600 series
    [1201.dwg, 1600.dwg, 1601.dwg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]
2022-03-16 UPDATE 1121
    Flipped LED PINS to the proper orientation
    [1121.dwg]
2022-03-16 Added too low/high failure code
    [phases.cpp, phases.h, playvideo.py]
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2022-03-21 Create BLOCK.DIAGRAM.dwg
    uploaded block diagram
    [BLOCK.DIAGRAM.dwg]
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2022-03-25 converted drawings to PDF, combined to final PDF
    [1100.dwg, 1220.dwg, 1601.dwg]
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2022-04-11 Final version of audio updated.
    Phone is working at 100% as of now, no errors produced
    [sam_FILE.ino]
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2022-04-22 led and audio fixes
    [phases.cpp, phases.h]
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2022-04-25 Commented out phone audio for time being
    Phone is cause of servo motors not working, commented out to flesh out other aspects of project.
    WITH THIS UPDATE:
    -ALL SERVOS WORKING
    -STEPPER MOTOR MOSTLY WORKING
    -7-SEGMENT WORKING MOSTLY
    -MAIN SWITCH INTERRUPT WORKS, PHONE SWITCH WORKS, ALL LEDS WORK
    [phases.cpp, phases.h]
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2022-05-03 stepper motor issues
